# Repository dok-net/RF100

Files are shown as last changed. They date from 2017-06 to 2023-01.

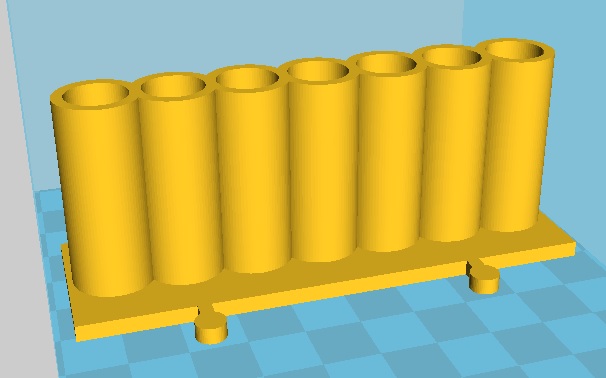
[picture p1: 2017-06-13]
3D Models/VariousObjects/BatteryHolderAAA/BatteryHolderAAA.JPG

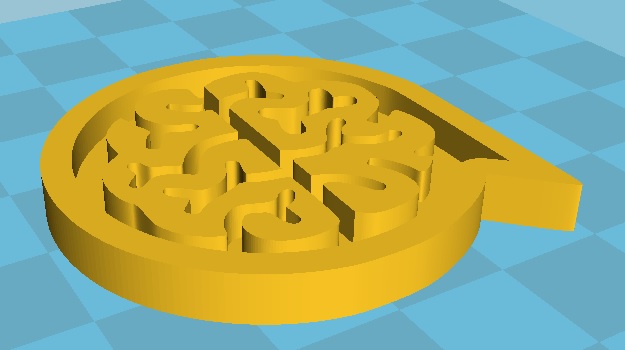
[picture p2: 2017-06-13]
3D Models/VariousObjects/TekkieBrain/TekkieBrain.jpg

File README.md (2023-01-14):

# [dok-net/RF100](https://github.com/dok-net/RF100/)

This is a repository with all Conrad documentation, the SD card contents,
and the latest Cura releases plus the RF100 V1 and V2 configuration files for it.

## Setup Guide
A link to the latest Cura release can be located in the 
`Software/Windows` or `Software/Mac` directory of this repository.
After installing, please do not chose to start Cura immediately, but rather
perform the following steps first.

In the same directory as the Cura setup file, there is a
`renkforce_rf100.def.json` printer definition file. Replace this
for the original printer definition file of the Cura installation, which is
located in `Program Files/Ultimaker Cura */share/cura/resources/definitions`.
Also copy the `renkforce_rf100_v2.def.json` and `renkforce_rf100_xl.def.json`
printer definition files for the RF100 V2 and the XL to the same location.
Then copy the extruder definition files `renkforce_rf100_extruder_0.def` and
`renkforce_rf100_xl_extruder_0.def.json`, both belong
into `Program Files/Ultimaker Cura */share/cura/resources/extruders`.

Next, start the Cura application, and in the pop-up window opened via
the menu item `Preferences/Configure Cura...`, select `Profiles`, and
then `Import` the custom profiles locate in this repository's `Config/Windows`
or `Config/Mac` directory.

For the default material selection of the RF100, PLA, you will then probably
want to `Activate` the custom profile `Config-PLA` as your default profile.

## Firmware Guide
The RF100 printer runs the Open Source [Marlin](http://marlinfw.org/) firmware.
The most obvious advantage of switching to the updated community-configured
version of Marlin versus the RF100 v1 is the increased print space, from 100mm
to 105mm, 110mm and 105mm in x/y/z dimensions, respectively. If you own the
RF100 v2, the only update in the stock firmware sources published by Conrad
actually was just this print space declaration, 120mm cubed for that printer.

After flashing new firmware to your printer, please reset the EEPROM to defaults
via the appropriate menu item under `Control`.

### Downloading pre-built firmware file to your RF100
In the menu bar, locate the `Settings` drop-down menu, select `Printer`,
then `Manager Printers...`. When you select your RF100 V1, V2, or XL printer
and push the `Update Firmware` button, the remaining steps should be
self-explaining. Use the matching firmware hex file for your printer version
provided here in the `Software/Firmware` folder. The `RF100 V1.1.cpp.hex` or
`RF100 V2.2.cpp.hex` firmware are the official ones provided by Conrad. For
updated community firmware, that for instance is based on much more recent
Marlin releases, choose among the RF100 Marlin hex firmware binaries.

### Build from source and flash in Arduino IDE (or compatible IDE)
If you have some familiarity with the Arduino IDE, this should be quite simple.
For V2 of the RF100, insert V2 into the repository names/branches/directory names
as appropriate.

Obtain the sources from the Github repository
[dok-net/Marlin](https://github.com/dok-net/Marlin/tree/renkforce_rf100_v2).
There should be a version tag that mimics the version tag in this repository,
like our version `v2.2-pre` is matched by `rf100-v2.2-pre` there.
Use this if you want to inspect the sources or rebuild the same binary firmware
as included here.
Please install the [LiquidCrystal](https://www.arduino.cc/en/Reference/LiquidCrystal)
library.
Copy the contents of the `Marlin/example_configurations/Renkforce/RF100` folder
into the Marlin folder.
Select this in the board manager: `ATmega2560 (Mega 2560) (Arduino/Genuino Mega)`.
Build the `Marlin.ino` project.

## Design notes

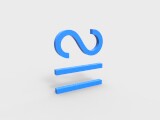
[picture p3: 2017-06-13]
3D Models/Mathematical symbols/Approximately equal to/approximately equal to.jpg

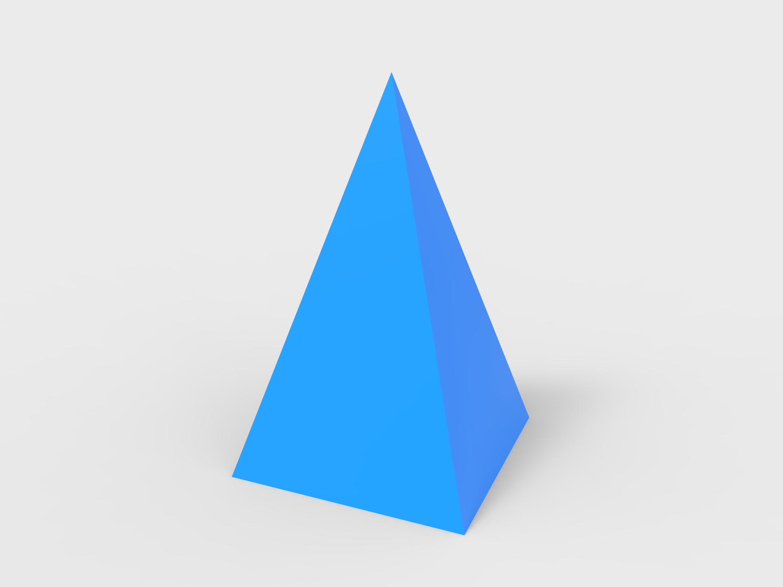
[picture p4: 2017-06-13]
3D Models/Basic shape/Four pyramid/Four pyramid.jpg

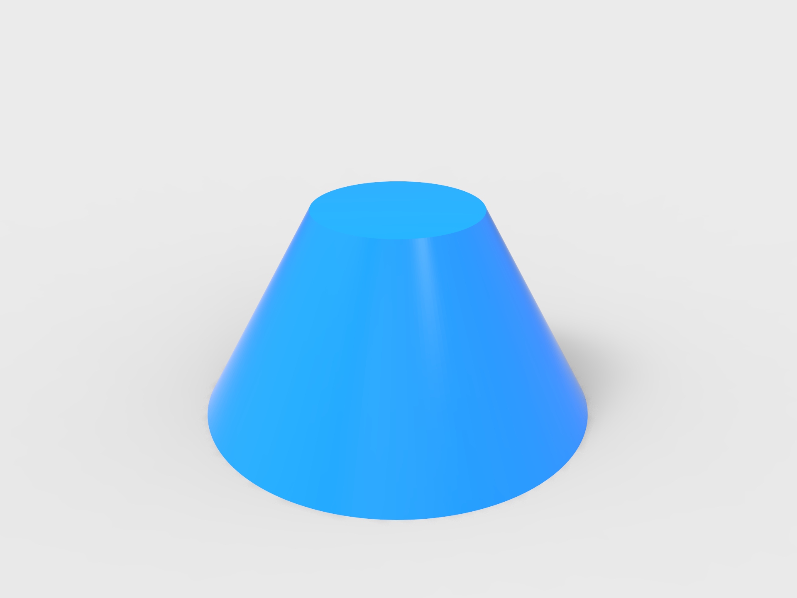
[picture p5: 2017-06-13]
3D Models/Basic shape/Frustum of a cone/Frustum of a cone.jpg

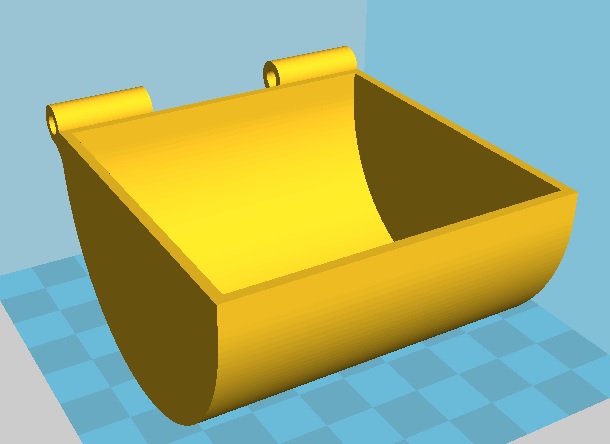
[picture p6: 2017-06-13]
3D Models/VariousObjects/TreasureBox/Box_top_cover.jpg

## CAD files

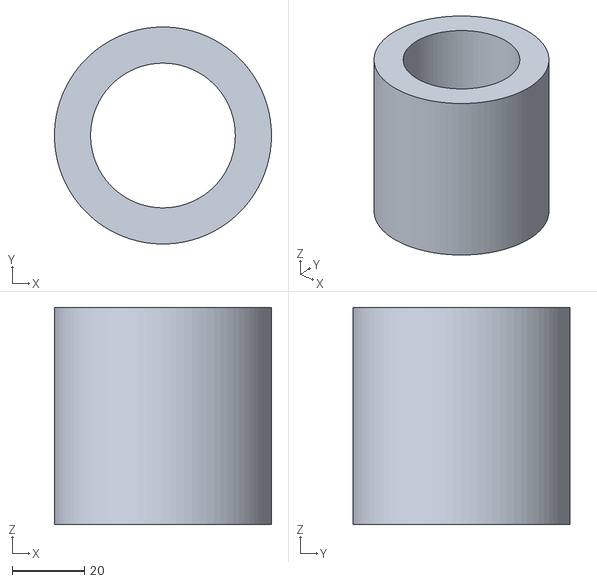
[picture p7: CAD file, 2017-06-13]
3D Models/Basic shape/Circular tube/Circular tube .stl
60.0 x 60.0 x 60.0

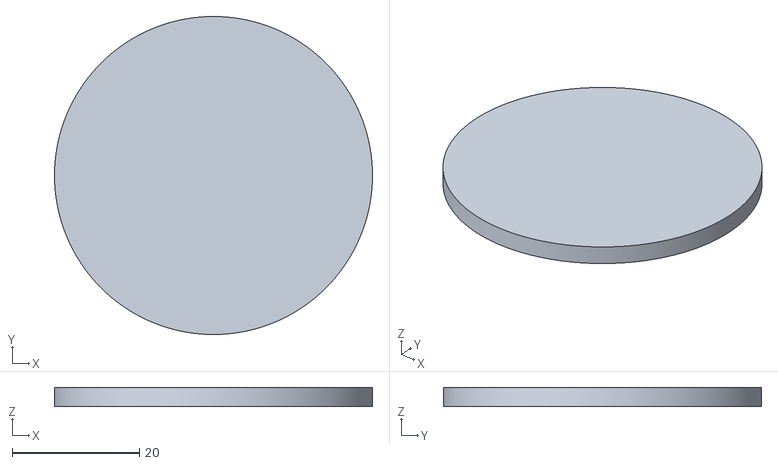
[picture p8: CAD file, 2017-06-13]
3D Models/Basic shape/Circular/Circular.stl
50.0 x 50.0 x 3.00

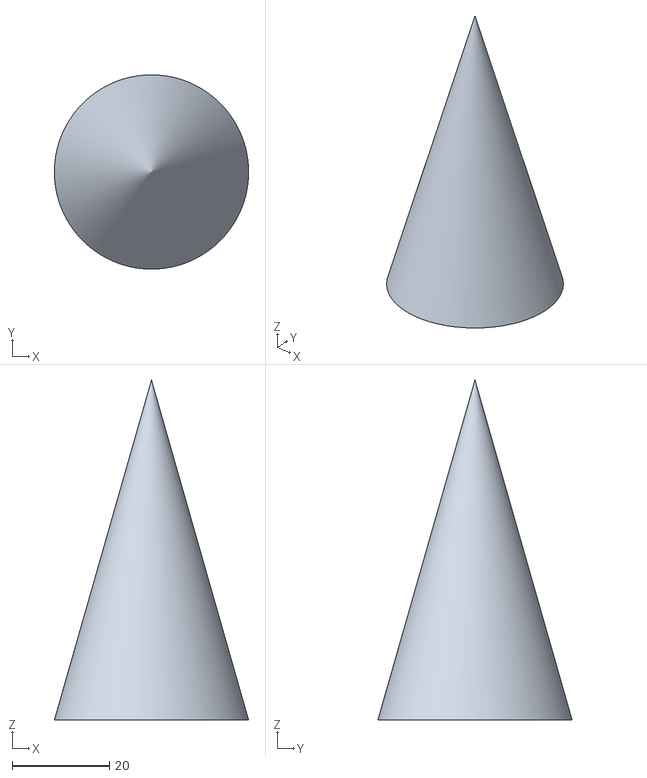
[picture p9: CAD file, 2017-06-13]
3D Models/Basic shape/Cone/Cone.stl
40.0 x 40.0 x 70.0

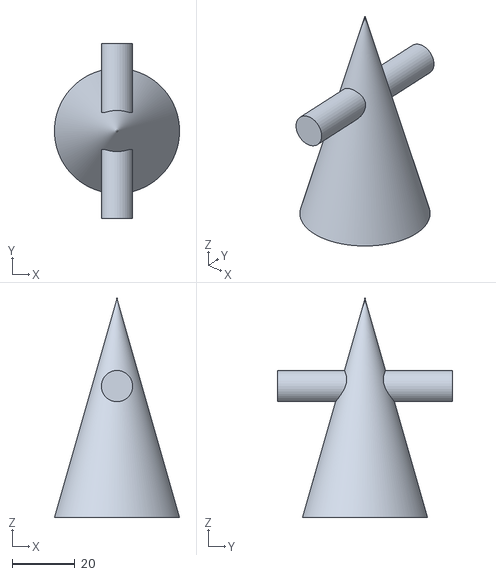
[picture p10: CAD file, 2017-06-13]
3D Models/Basic shape/Conical and cylindrical/Conical and cylindrical .stl
40.0 x 56.0 x 70.0

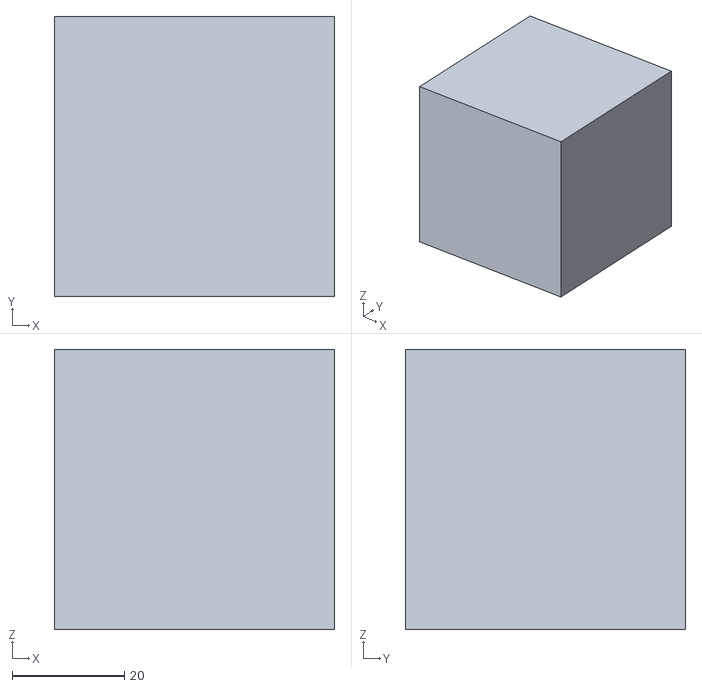
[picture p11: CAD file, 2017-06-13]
3D Models/Basic shape/Cube/Cube.stl
50.0 x 50.0 x 50.0

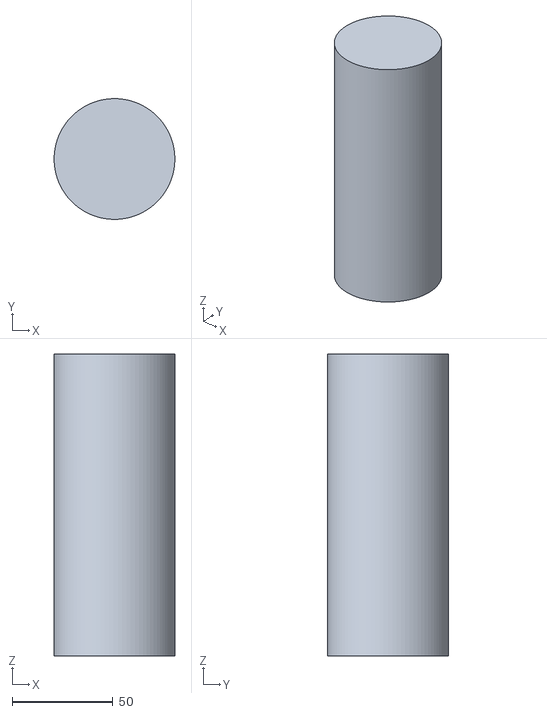
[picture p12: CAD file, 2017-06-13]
3D Models/Basic shape/Cylinder/Cylinder.stl
60.0 x 60.0 x 150.0

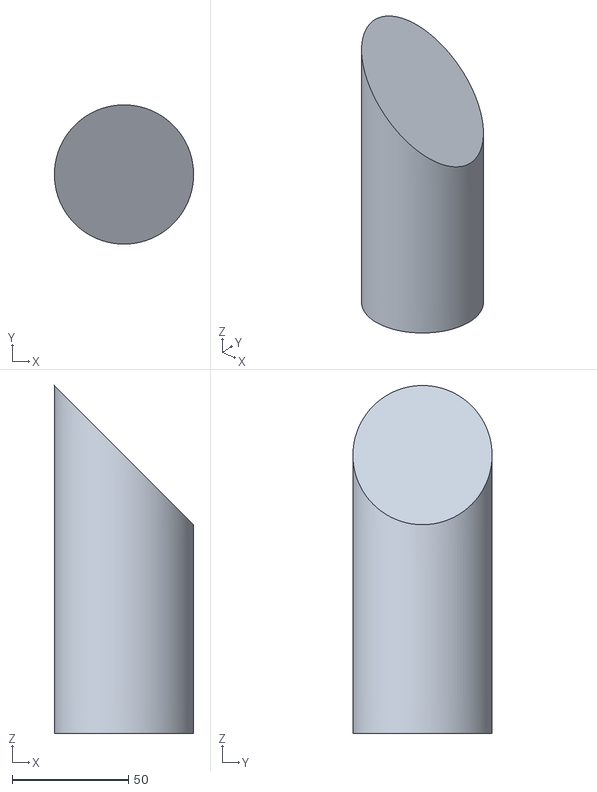
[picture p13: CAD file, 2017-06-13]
3D Models/Basic shape/Cylindrical cutting/Cylindrical cutting .stl
60.0 x 60.0 x 150.0

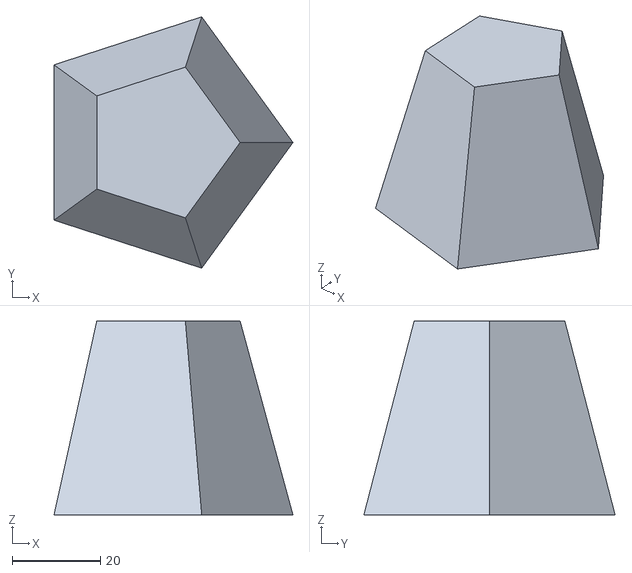
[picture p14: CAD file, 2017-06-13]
3D Models/Basic shape/Five squaretable/Five squaretable.stl
54.3 x 57.1 x 44.0

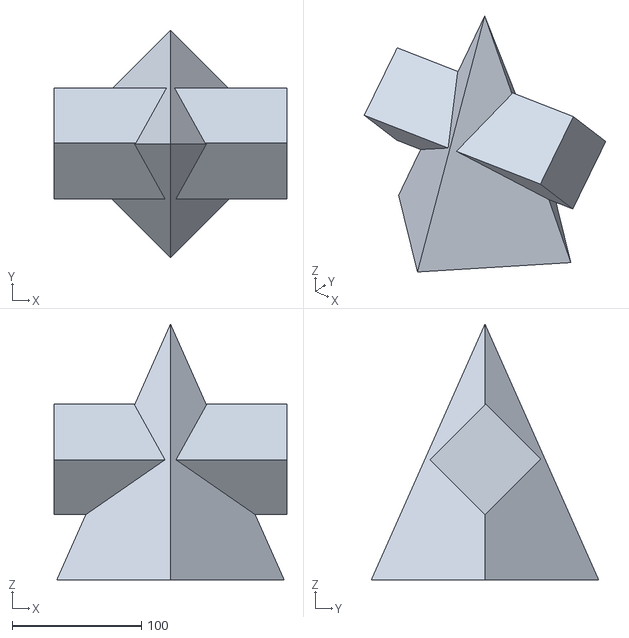
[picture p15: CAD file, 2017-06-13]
3D Models/Basic shape/Four pyramid + cuboid/Four pyramid + cuboid.stl
180.0 x 176.0 x 198.0

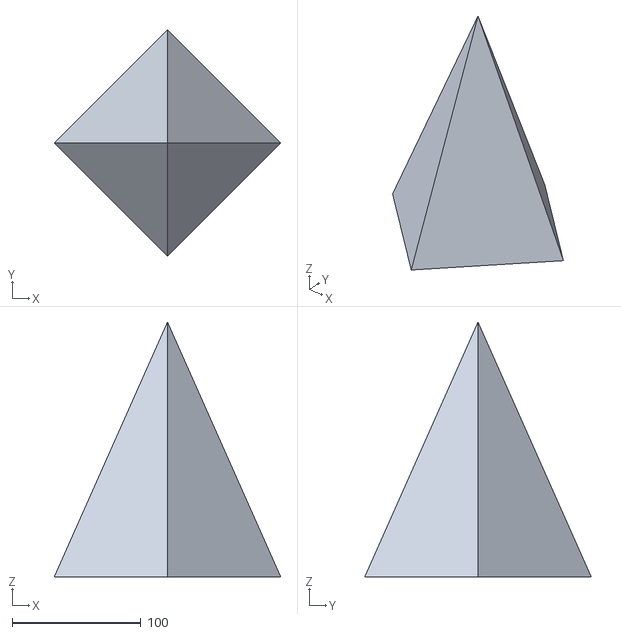
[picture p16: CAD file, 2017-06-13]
3D Models/Basic shape/Four pyramid/Four pyramid.stl
176.0 x 176.0 x 198.0

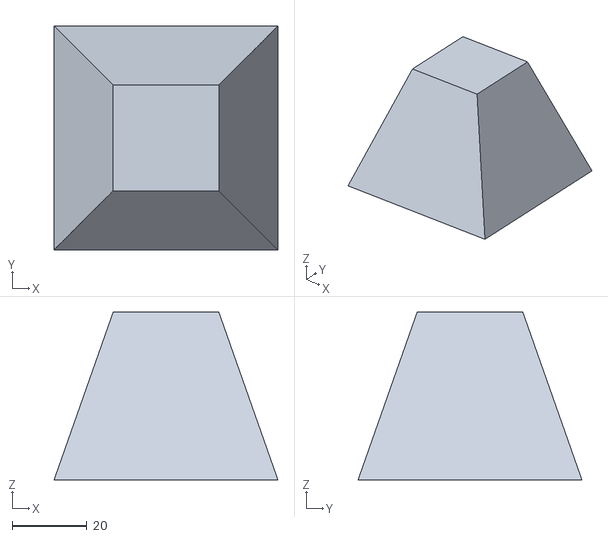
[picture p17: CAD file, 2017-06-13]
3D Models/Basic shape/Four squaretable/Four squaretable.stl
60.0 x 60.0 x 45.0

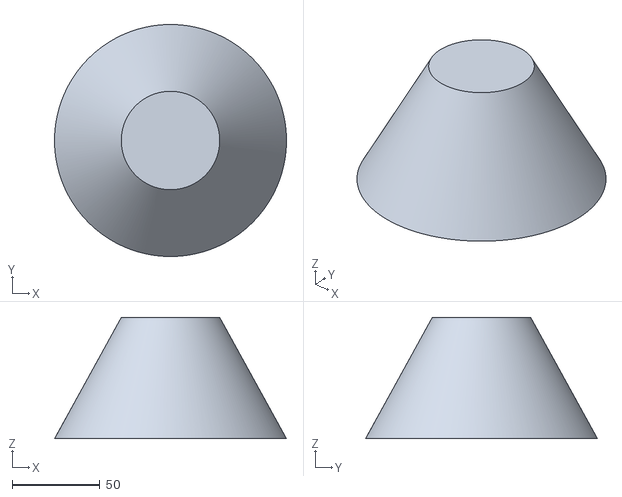
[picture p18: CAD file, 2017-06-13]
3D Models/Basic shape/Frustum of a cone/Frustum of a cone.stl
132.0 x 132.0 x 69.0

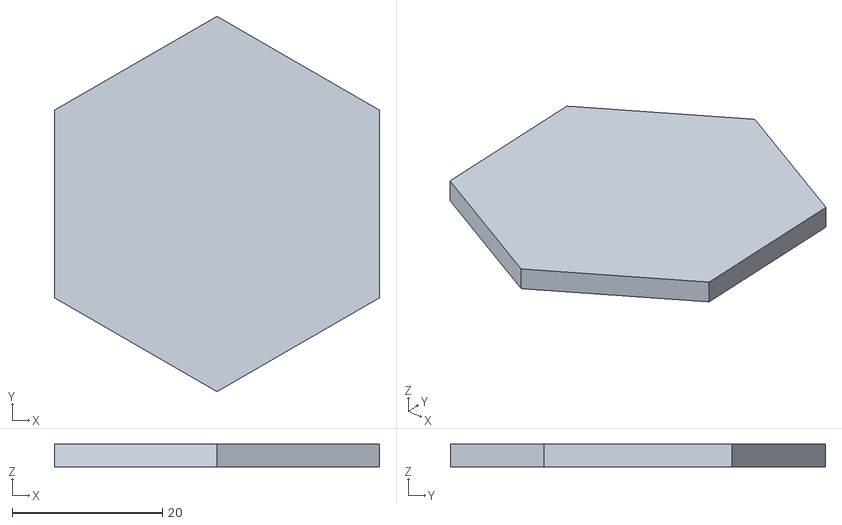
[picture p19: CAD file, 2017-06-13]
3D Models/Basic shape/hexagon/hexagon.stl
43.3 x 50.0 x 3.00

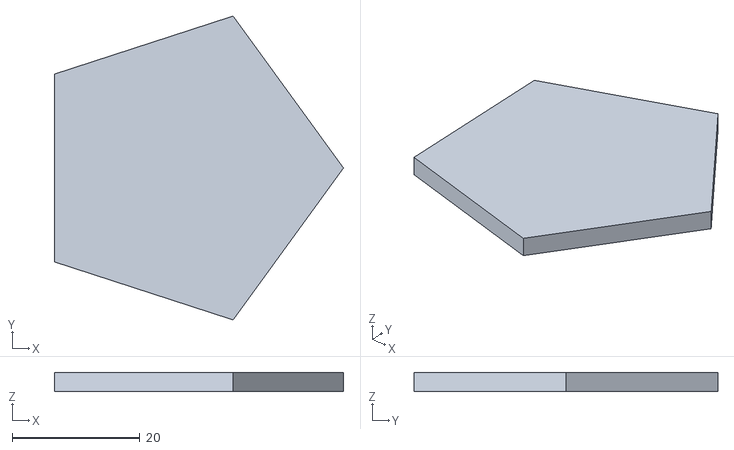
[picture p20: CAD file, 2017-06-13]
3D Models/Basic shape/Pentagon/Pentagon.stl
45.2 x 47.6 x 3.00

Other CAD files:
3D Models/Basic shape/pentagonal pyramid/pentagonal pyramid.stl
3D Models/Basic shape/rectangle/rectangle.stl
3D Models/Basic shape/Rectangular block/Rectangular block.stl
3D Models/Basic shape/Ring/ring.stl
3D Models/Basic shape/Six squaretable/Six squaretable.stl
3D Models/Basic shape/Sphere/sphere.stl
3D Models/Basic shape/Square/square.stl
3D Models/Basic shape/Three pyramid/Three pyramid.stl
3D Models/Basic shape/Three squaretable/Three squaretable.stl
3D Models/Basic shape/Trapezoidal/trapezoidal.stl
3D Models/Basic shape/Triangle/triangle.stl
3D Models/Basic shape/Two rectangular bodies/Two rectangular bodies.stl
3D Models/Capital letters (A-Z)/A.stl
3D Models/Capital letters (A-Z)/B.stl
3D Models/Capital letters (A-Z)/C.stl
3D Models/Capital letters (A-Z)/D.stl
3D Models/Capital letters (A-Z)/E.stl
3D Models/Capital letters (A-Z)/F.stl
3D Models/Capital letters (A-Z)/G.stl
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

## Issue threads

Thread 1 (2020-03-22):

Source code for RF100 V2 Marlin 2.0.4.4.hex

piotrkochan, 2020-03-22:
HIi great work!
Could You share RF100 V2 Marlin 2.0.4.4.hex source code? Or at least Configuration.h?
Thanks

piotrkochan, 2020-03-22:
I've found it https://github.com/dok-net/Marlin/tree/renkforce_rf100_v2

piotrkochan, 2020-03-22:
I'm reopening the issue because Marlin 2.0 Configuration.h and adv is unpopulated.
https://github.com/dok-net/Marlin/blob/2.0.x-renkforce_rf100/Marlin/Configuration.h

dok-net, 2020-03-22:
This time you're taking too long to find your mistake by yourself :-)
Hint: https://github.com/dok-net/Marlin/blob/rf100-v3.0.6/config/README.md

Closed 2020-03-22.

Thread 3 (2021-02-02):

Please, i need help quickly ||  Bitte, ich brauche schnell Hilfe

hapi-dev, 2021-02-02:
Hello, i have rf100 printer but i updated firmawre to v1.1 and filament change doesnt work. Where can i find rf100 v1.0 firmware!
If you have please send me to email: august2mcon@gmail.com

GERMANY:
Hallo, ich habe rf100 Drucker, aber ich habe firmawre auf v1.1 aktualisiert und Filamentwechsel funktioniert nicht. Wo finde ich die Firmware von rf100 v1.0?
Wenn ja, senden Sie mir bitte eine E-Mail an: august2mcon@gmail.com

dok-net, 2021-02-12:
@hapi-dev I would like to invite you to install the latest version of the firmware for your RF100 V1, V2, or XL from here. Besides, I don't recall noticing any difference in the filament unload feature when updating from "Renkforce's" release 1.0 to 1.1. I can't help you with the 1.0 firmware, but never mind, just upgrade to what's offered here. It's a bit different, as Marlin has evolved quite a bit, and the Renkforce firmware was heavily modded, but once you do, you're part of the open-source ecosystem :-)

Closed 2021-02-12.

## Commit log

2017-06-13 RF100 SD Card Contents-Version05(20170214)
    [0.stl, 1.stl, 2.stl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]
2017-06-13 Updated printer definition file for CURA for Mac
2017-06-13 Printer definition and material profiles updated for Cura 2.5.0
2017-06-23 New Cura 2.6.0 release for Windows.
    After install, before first start, copy renkforce_rf100.def.json to Program Files\Cura 2.6\resources\definitions (may require administrator privileges)
    In menu Preferences/Configure Cura.../Profiles, import the .curaprofile material profiles.
2017-07-25 Add firmware V1.1, official downloadable build, dated Tuesday, ‎20 ‎June, ‎2017, ‏‎09:26:58
2017-09-01 Material profiles updated with Cura 2.7.0
2017-09-08 Reviewed printer definition file in Github Ultimaker/Cura repository commit 4b4f971222a1d7c65679b416d4c3113b7a1c1483 and merged in.
2017-09-08 Reverse order of moving platform down and moving head to min endstops, seeing the head move closely across the platform surface for very thin prints freaks me out.
2017-09-08 Minimize oozing of filament on start and after end.
2017-09-08 Retracting filament while heating is still on seems safer.
2017-09-09 Optimize travel speeds and filament retraction and extrusion in start and end code.
    The filament is extracted in the origin position to place a small dot on the build plate.
    From there, a very fine thread of filament will be draws to the object starting position,
    which does not interfere with the printing, but assures that there is enough filament in
    the print head when the print begins.
    On end, the retraction relieves pressure just enough to reduce oozing, but leaves enough
    filament in the print head.
    Where recalibrating the build plate, remove excess filament from the nozzle, otherwise this
    will increase the offset to the build plate surface while recalibrating the cold printer.
2017-09-09 Proper Z height on startup to avoid spreading filament on build platform.
2017-09-13 Disposing extra filament in start code stays below gantry height.
2017-10-28 Tested in back-to-back printing. Some manual intervention is required for a good start: during heat-up, some filament oozes from the hot head, pluck this off if possible, then there is no excess fila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
2017-10-31 More back-to-back printing improvements.
2017-11-28 Initial feed tuned. Raft for large bottom area didn't stick to print bead, increase raft margin and lower base thickness to improve adhesion.
2017-12-13 Refresh profiles - some overrides were hiding improvements in printer settings.
    Improved raft smoothness, adhesion and ease of removal.
2018-08-21 Cura 3.4.1 64 bits released for Windows & Mac.
    The links currently don't work, but locating the download from there is trivial.
2019-02-12 Profiles were overriding support and raft settings with old values,
    causing both to stick too hard to the print.
2019-02-13 Minimize profile overrides vs. RF100 common printer settings.
2019-03-14 Added profile to support PETG filaments. There are many manufacturers that offer PETG filaments that can be printed around 210°C.
2019-03-23 Top and bottom thickness overrides removed from RF100 profile, defaults are 0.1mm thicker.
    Inflill and support lines made 0.1mm wider, especially with PETG they were not solid and collapsed.
2019-08-14 Merged and rebuilt RF100 community and Marlin1.1.6 sources.
2019-08-14 Rebased firmware source tree to Marlin 1.1.9 and rebuilt.
2019-10-07 Firmware build for release v2.4 - hardware safety fix:
    Value for maximum z reduced from 110mm to 108mm,
    print bed was mechanically jaming on rehome after power cycle
    if the previous job by default had moved the print bed all the way down.
2019-10-16 Firmware patch rf100-v2.5 fixes underextrusion, was feeding only 9.2mm for 10mm. This solves mystery of previous
    flow correction at 110% in Cura configuration...
2019-10-18 Filament retraction corrected in Cura file to same value as in firmware (3.0mm)
2019-10-18 Conrad firmware for RF100 V2 added.
    Marlin 1.1.9 updated firmware for RF100 V2 added.
2019-10-19 Next attempt to fix extended build space: Z max, power cycle, new print - build plate crashes into bottom.
2019-10-23 Lower extruder auto-fan start temperature to 50°C, it is commonplace.
2019-10-25 Firmware: Enable PID autotune menu, and implement tuning results in firmware.
    Tuning was performed on plain RF100 V1 and RF100 V2 with case, then averaged.
2019-10-29 High printing temperature causes excessive stringing on hops.
2019-10-29 Reslice RF100 sample
2020-01-01 Increase brim width for proper adhesion of narrow objects.
    Marlin V2.0.1 release.
2020-01-02 Prime print head settings for RF100, RF100 V2. Drop from RF100 XL because I don't have one to take measurements.
2020-01-03 No extrusion issues printing PETG at 5mm/s
2020-01-03 No melting issues at 1s per layer printing a 1.4mm x 1.4mm cuboid with notches every 5mm.
2020-01-03 Retract 5mm instead of 3mm, Ultimaker direct drive extruders work at even 6.5mm.
    The increased retraction speed exacerbates stringing.
2020-01-28 Marlin V2.0.2 release builds.
2020-02-02 Marlin V2.0.3 release builds.
2020-02-29 Marlin V2.0.4.4 release builds.
2020-06-03 Marlin V2.0.5.3 release builds.
2021-02-13 Marlin V2.0.7.2 release plus bug fixes builds.
2021-02-13 Updated printer definitions from PR CURA-6711_support_structure_dropdown #8055
2022-04-09 Ultimaker Cura release 4.13.1.
    Marlin release V2.0.9.3.
2023-01-07 Fixed installation Path
    see: https://community.ultimaker.com/topic/40678-printer-profiles-meta-settings/?do=findComment&comment=308267
